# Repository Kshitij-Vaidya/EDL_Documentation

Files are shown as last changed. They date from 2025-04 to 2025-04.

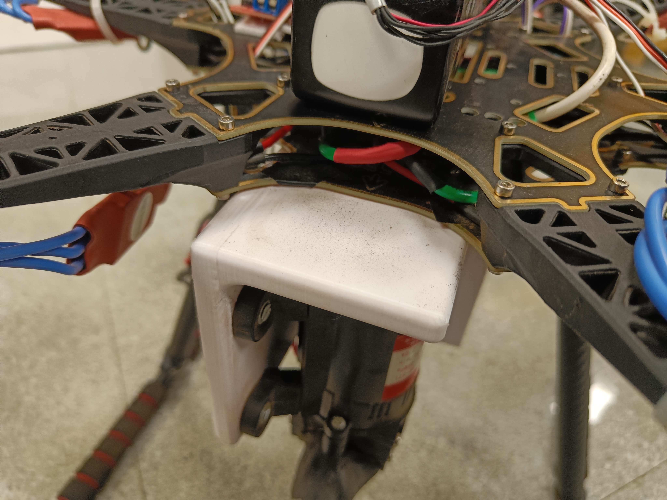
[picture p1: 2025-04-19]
others/assembly/close_up_motor_clamp.jpg

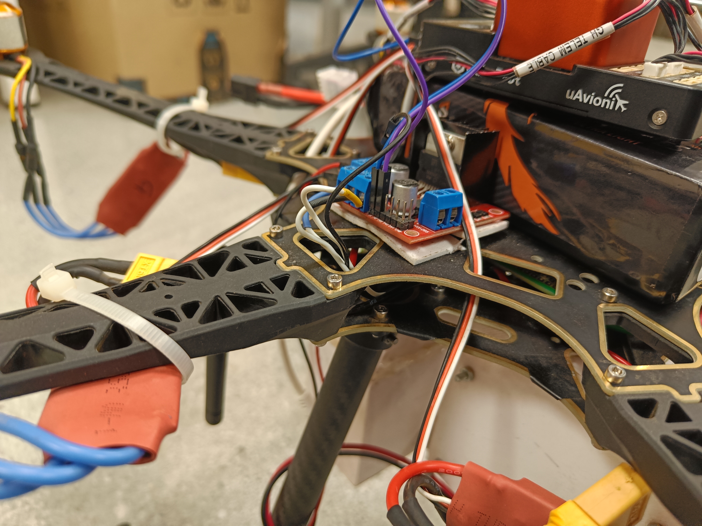
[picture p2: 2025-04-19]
others/assembly/arm_attachments.jpg

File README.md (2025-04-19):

# EDL 2025 Project Submission Repository

## Project Overview

### Project Name: P08 - Wall/Glass Pane Cleaning Drone
### Team Number: MON-13
### Team Members:
| Name | Roll No  |
|---|---|
| Aagam Shah | 22B1201  |
| Adit Srivastava | 22B1269  |
| Jainam Ravani | 22B1242  |
| Jay Mehta | 22B1281  |
| Kshitij Vaidya  | 22B1829  | 

<!-- ### Problem Statement and Solution: -->

## Problem Statement 
1. Build an aerodynamically stable drone for cleaning high-rise building windows.  
2. Ensure it can withstand windy conditions and recoil from high-pressure water spraying.  
3. Carry sufficient water to clean multiple windows.  
4. Operate safely in both manual and autonomous modes.  

## Proposed Solution

Our system consisted of a water spraying mechanism integrated with a baseline drone model. The spraying mechanism comprises of an onboard pump capable of ejecting water at 3L/min, which when coupled with our chosen nozzle suffices to clean dust and grime from glass surfaces, and a water tank that can either store enough water for the mission or utilize a continual water supply from a ground pump.

### Hardware Design Choices

In order to sustain the additional payload, we used an S550 hexacopter frame; the specs of various components including the BLDC motors and propellers were decided so as to achieve stable hover at 50% throttle. Pixhawk Cube flight controller equipped with PX4 Autopilot was used for regulating motor speeds to achieve a controlled flight. Various flight modes of the PX4 Autopilot were used to achieve manual as well as semi-autonomous navigation. Manual operation consisted of navigating the drone using roll, pitch, yaw and throttle setpoints from a Radio Controller; whereas the autonomous mode consisted of navigating to prespecified waypoints set by the user on the Ground Control Station (QGroundControl).

### QGroundControl Software

QGC proved to be instrumental not only for communication with the drone during flight but also for calibrating sensors, motor ESCs and updating flight parameters. For establishing connection with the Ground Control Station, we used a radio telemetry module. The state estimates of the drone required for autonomous navigation were determined using an external GPS module and onboard sensors on the flight controller. For remotely operating the spraying mechanism, an RC channel was assigned to regulate the voltage of the onboard pump.

An optimal choice of various PID gains for the flight controller ensured that our drone remained stable during flight, and maintained its position even in the presence of external disturbances like wind and recoil force of the spray. For aiding manual navigation, FPV control was added by using a Raspberry Pi and an onboard RPi-camera for transmitting continuous video streams to the ground control station. Further, all electrical components were insulated using a silicone spray and were mechanically protected by 3D-printed envelopes.

### Safety Measures

To ensure safety of the drone, surrounding structures, and the operating personnel, various failsafes were enabled including GPS signal loss failsafe, low battery failsafe, and radio signal loss failsafe. These failsafes ensured that in any of the aforementioned conditions, the drone returns safely to its launching site. In addition to this, a pipeline was established to allow users to upload custom missions or specify a set of waypoints, enabling cleaning of an entire structure with a single key press.

## Project Deliverables

1. A Hexacopter Drone with an onboard Pixhawk Cube, Telemetry Module, GPS Module and Radio Receiver 
2. A Complete Water Spraying Mechanism with a Water Tank, Water Pump and a Spraying Pipe with a Nozzle for Effective Water Spraying
3. Complete Software Stack for operating the Drone using Radio Control as well as for autonomous takeoff and hover in various operating modes like Position and Hold.  

## Navigating the Repository

```plaintext
/
├── src/
│   ├── Controller 1
|   ...
├── 3d_models/
│   ├── Component 1
│   ...
├── pcb/
│   ├── others/
├── reports/
├── others/
├── bom.xlsx
└── README.md
```

The repository includes all the essentials needed to understand and replicate this project in its current state. We have also highlighted our learnings, the mistakes we have made and the solutions and workarounds that we have found. 

1. The `src` folder includes the details of our Pixhawk, Raspberry Pi and the Radio Control that we have used. Their respective `README.md` files include instructions of using them and what changes we made to their default configurations before operating them.
2. The `3d_models` directory has all our CAD Models with their renders and the images of final fabricated components. We also include our insights about each of these components and design choices(if any) that went into finalising said components.
3. While we did not design and fabricate a PCB, the `pcb` directory includes a single directory `others` that has the designs and implementations and schematics of our in-house Power Distribution Board and the BEC Circuit that we have installed on our current prototype.
4. `reports` includes all our checkpoint presentations. This directory serves as a progress tracker for our project which indicates the levels of completion of our drone at various stages of the semester.
5. We include our simulation results and images of our assembly in parts and as a whole in the `others` directory. 
6. The `bom.xlsx` is our complete Bill Of Materials where we provide the list of components that have been procured for the project. We have also provided links and references for purchase from official and authentic sources.    

## Learnings and Key Takeways

1. Developed an understanding on aerial robotics (specifically quadcopters and hexacopters) from a mechanical point of view. This was crucial in making the choice between a quadcopter and hexacopter for out final drone. We eventually settled on the latter because of its increased payload capacities.
2. Working with the Pixhawk Cube as our Primary Flight Controller. This was a unique challenge as despite the Pixhawk being an off-the-shelf state of the art controller, we ran into multiple techincal and compatibility issues that needed to be resolved. We also needed to re-configure the boot sequence of the Pixhawk to ensure that our ESC Calibration and power up was synchronised
3. Electronic Speed Controllers must be thoroughly tested before installation on the drone. We faced severe troubles with the calibration of our ESCs partly because of the faults in the ESCs themselves and partly because of their improper calibration with the flight controller
4. Power Distribution Boards are extremely crucial in robotics applications. Our on-frame PDB was not uniformly powering the ESCs causing them to shut down unexpectedly. This also cost us one of our ESCs as it shut down during testing and we were unable to get it working again. To resolve this issue, we developed and made our own PDB using single sided copper clads and multi-stranded PVC wire.  
5. Experimented with different methods of operating the drone including Radio Control, using the QGroundController and operating the actuators from a laptop communicating with the drone using a Telemetry Module. These were especially useful for continuous testing and dry testing the components before performing the flight tests
6. Beyond the technical learnings, this project also helped us improve our time management and team skills. Coordinating with other members to ensure that the project keeps moving forward and our progress is not halted. We also learned that tasks should not be trivialized or underestimated. We made this mistake with our assembly and calibration but ran into a large number of errors because of both our mistakes and the malfunctions of our components. 

## Road Ahead

In the semester long project, we were able to develop a proof of concept prototype for the window cleaning drone but there are several areas of improvement that we have identified which would make this project even better:

1. Our current payload capacity is around 2kg which includes a 0.5L water tank. This is not sufficient for sustained cleaning purposes and we need to increase the total water carrying capacity of the drone. This can be done in 2 ways : increasing the water tank capacity or using a ground stationed water pump to supply water to the drone. Both these methods can be experimented with, each has their advantages and disadvantages which must be weighed carefully.
2. We can use motors with an inceased KV Rating. This increases the total thrust that is provided by the motors and thus increases the payload capacity of the drone. While this comes at the cost of a decreased battery life, the analysis of the decision must be done by weighing all options such as exploring the possiblility of using a larger battery
3. The whole drone system can be scaled by in size. While the weight of the drone frame does increase, this can be offset by using larger batteries and more powerful motors. This also facilitates a larger water tank which can be installed on-board. (In the current marker agricultural and irrigation drones which work on similar principles have payloads of upto 10-16L of fluid)
4. Implement a user-friendly Graphical User Interface Application that can be used to input the coordinates of the windows as waypoints with approximate window sizes. An on-board computer converts these into a mission which can be run by the drone to clean the windows at the waypoints in succession. 
5. We can modify and explore robust controllers which provide additional stability to the drone and improve the performance of the drone in windy conditions and handle the recoil and other forces by the water mechanism in a better manner

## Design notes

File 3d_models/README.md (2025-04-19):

# 3D Models
## File Structure

```
3d_models/
├── Canopy/
│   ├── canopy.png
│   ├── canopy.stl
│   └── README.md
├── Clamp for Diaphragm Pump/
│   ├── diaphragm_pump_clamp.png
│   ├── diaphragm_pump_clamp.stl
│   └── README.md
├── PixHawk_Casing/
│   ├── pixhawk_casing.png
│   ├── pixhawk_casing.stl
│   ├── Section-Analysis.png
│   └── README.md
├── Raspberry Pi Casing Bottom/
│   ├── rpi_casing_bottom.png
│   ├── rpi_casing_bottom.stl
│   └── README.md
├── Raspberry Pi Casing Top/
│   ├── rpi_casing_top.stl
│   ├── rpi_casing_top.png
│   └── README.md
├── Tank_Container/
│   ├── tank_container.png
│   ├── tank_container.stl
│   └── README.md
└── Tank_Cover/
    ├── tank_cover.png
    ├── tank_cover.stl
    └── README.md
```

## Material Used
ABS is used for all the models as it is significantly stronger than PLA and water doesnt seep through it as much as it does through ABS thus helping us make water-tight container. We had used PLA initially for some models but it wasn't very strong.

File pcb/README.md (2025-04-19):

# PCB Directory

This directory is named for convention but **does not contain any PCB (Printed Circuit Board) design files**, as our project does not utilize traditional PCBs.

Instead, we have developed:
- An **in-house Power Distribution Board (PDB)** tailored specifically for our drone’s power routing needs.
- A **custom Battery Eliminator Circuit (BEC)** to efficiently provide regulated voltage to onboard components.

All power management is handled through these custom solutions, allowing for greater flexibility and simplified integration with our drone architecture.

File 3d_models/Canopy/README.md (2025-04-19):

## Canopy

### Placement
The canopy is mounted directly above the top plate of the drone and is secured using adhesive(double-sided) tape applied to the top plate.

### Function
- **Protection:** It safeguards the upper components of the drone from physical impact, dust, and water ingress.
- **Aerodynamics:** It contributes to improved aerodynamic performance by streamlining the top surface of the drone.

### Material
Constructed from **ABS (Acrylonitrile Butadiene Styrene)**, a durable and impact-resistant thermoplastic ideal for lightweight protective applications.

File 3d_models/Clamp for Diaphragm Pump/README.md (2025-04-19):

## Clamp for Diaphragm Pump

### Placement
This is an L-shaped clamp designed with one face mounted to the bottom plate of the drone, while the other face secures the diaphragm pump in an upright position.

### Function
The clamp’s sole function is to provide firm and stable support for the diaphragm pump, ensuring it remains upright during operation.  
To withstand mechanical stress and potential impact, the clamp is printed with **100% infill**. This structural density is critical, as previous iterations with lower infill failed under impact conditions.

### Material
Manufactured from **ABS (Acrylonitrile Butadiene Styrene)** for its high strength, durability, and impact resistance.

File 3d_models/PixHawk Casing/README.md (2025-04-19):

## PixHawk Casing

### Placement
The casing is designed to fit securely over the PixHawk flight controller. The square cavity is dimensioned to enclose the PixHawk Cube precisely.

### Function
- **Protection:** Shields the PixHawk Cube from physical damage.
- **Stability:** Helps keep the flight controller securely in place during operation.
- **Dust Prevention:** Covers the exposed ports of the PixHawk, reducing the risk of dust ingress.

### Material
Fabricated from **ABS (Acrylonitrile Butadiene Styrene)**, chosen for its robustness, durability, and impact resistance.

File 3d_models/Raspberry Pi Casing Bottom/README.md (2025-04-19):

## Raspberry Pi 4 Casing — Bottom

### Placement
The Raspberry Pi 4 is mounted into this bottom casing and secured using nuts and bolts. Side extrusions are incorporated into the design to interlock with the top part of the casing, ensuring a snug fit.

### Function
- **Protect** the Raspberry Pi 4 from impact damage during drone operation.
- **Secure** the Raspberry Pi 4 firmly in place using fasteners, preventing internal movement that could lead to hardware damage.

### Material
Constructed from **ABS (Acrylonitrile Butadiene Styrene)**, selected for its high impact resistance and structural integrity.

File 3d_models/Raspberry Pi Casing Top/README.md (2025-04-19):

## Raspberry Pi 4 Casing — Top

### Placement
This component fits directly on top of the Raspberry Pi 4, forming the upper half of the protective enclosure. It includes dedicated slots to accommodate the ribbon cable of the Raspberry Pi NoIR Camera.

### Function
- **Protect** the Raspberry Pi 4 from impact and environmental exposure.
- **Allow Connectivity** by providing access points for the NoIR Camera ribbon strip without compromising enclosure integrity.

### Material
Made from **ABS (Acrylonitrile Butadiene Styrene)**, chosen for its durability, impact resistance, and suitability for electronic housings.

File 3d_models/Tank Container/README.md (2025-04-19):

## Tank Container

### Placement
The tank container is affixed to the bottom rim of the tank cover using adhesive. A hole is drilled at the base of the container to accommodate an extrusion, which connects to the pipe leading to the diaphragm pump.

### Function
This component functions as the **primary water storage unit** for the drone. Its dimensions are constrained by:
- **Payload capacity** of the drone
- **Ground clearance** to ensure safe landing and operation

### Material
Fabricated from **ABS (Acrylonitrile Butadiene Styrene)** for its strength and moldability.  
A **conformal coating spray** is applied to the interior surface to ensure the container is both **water-proof** and **water-tight**.

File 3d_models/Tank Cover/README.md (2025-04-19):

## Tank Cover

### Placement
The tank cover is mounted on top of the tank container and is glued along the rim for a secure seal. It is further attached to the drone’s bottom plate using **2 cm spacers**, providing structural stability and elevation.

### Function
- **Seals** the tank container to prevent water leakage.
- **Provides Access** through a dedicated hole for filling the tank with water.

### Material
Constructed from **ABS (Acrylonitrile Butadiene Styrene)**.  
An internal application of **conformal coating spray** ensures the component is **water-proof** and **water-tight**, maintaining the integrity of the onboard water storage system.

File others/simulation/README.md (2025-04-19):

Before performing hardware tests, we validated our approach on simulation.

## Software Requirements
- Gazebo Classic : https://docs.px4.io/main/en/sim_gazebo_classic/index.html
- ROS2 : https://docs.ros.org/en/humble/Installation.html
- MicroXRCE DDS : https://micro-xrce-dds.docs.eprosima.com/en/latest/agent.html
- Plotjuggler : https://index.ros.org/p/plotjuggler/
- Python : Version 3.10 or higher
- QGroundcontrol : https://docs.qgroundcontrol.com/master/en/qgc-user-guide/getting_started/download_and_install.html

## Gazebo Simulator
Gazebo Classic is a powerful, open-source 3D robotics simulator that integrates with ROS (Robot Operating System) and allows realistic testing of robots in complex environments. It provides physics simulation (via engines like ODE, Bullet), sensor simulation (e.g., cameras, IMUs, lidars), and supports plugins for custom behavior. For simulating our system, we used a default hexacopter model available in PX4's software stack, and varied its physical parameters according to our hardware specifications. Some of these values are:

### Inertial Parameters

| Component | Dimensions | Mass  | MoI (Ix) | MoI (Iy) | MoI (Iz) |
|---|---|---|---|---|---|
| Chassis | 0.67 x 0.67 x 0.15 | 0.997  | 0.039 | 0.039 | 0.075 |
| Camera | 0.01 x 0.01 x 0.01 | 0.011  | 1.83e-7 | 1.83e-7 | 1.83e-7 |
| Landing Legs  | 0.01 x 0.03 (r x h) | 0.1 | 7.54e-4 | 7.54e-4 | 7.45e-3 |
| Rotors | 0.128 x 0.005 (r x h)  | 0.024  | 9.83e-5 | 9.83e-5 | 1.97e-4 |
| Nozzle | 0.05 x 0.12 (r x h) | 0.05 | 0.07 | 0.07 | 0.07 |

### Motor Parameters

| Parameters | Value |
|---|---|
| Time Constant (s) | 0.0125 |
| Max Speed (rad/s) | 1240 |
| Max Speed (RPM) | 11840 |
| Motor Constant (N·s²/rad²) | 8.038e-6 |
| Moment Constant (N·m·s²/rad²) | 9.55e-3 |
| Rotor Drag Constant | 0.09637 |
| Rolling Moment Coefficient | 1e-6 |

## Simulation Environment
- Simulator: Gazebo Classic
- Drone Model: Typhoon H480 (with custom parameters)
- Autopilot: PX4 v1.14
- Middleware: ROS2 with MicroXRCE bridge
- Operating System: Ubuntu 22.04

## Objective
- Take off the drone and maintain a constant altitude for 10s.
- To start spraying water in the specified direction.
- To ascend upwards by some distance while spraying water and
then stabilizing at its original altitude

## ROS2
We used ROS2 as the middleware for using the offboard mode on our simulated drone. A ROS2 node was run in the form of a python script after launching the drone. This node essentially utilized gazebo-ros topics for applying user-specified forces on the drone model. For bridging ROS2 with Mavlink (used by PX4 for communication), we used MicroXRCE-DDS.

## Water Spray Test
For simulating weight of the water column, reaction and recoil forces we applied forces in horizontal and vertical directions when the drone attained a stable altitude. The aforementioned script applied a constant vertical force simulating the weight of the onboard tank/ water column, and a user specified horizontal (with respect to drone frame) force on the drone.

## Running the Simulation
Expected configuration:
- All required softwares are installed
- Latest version of PX4 Autopilot repository is cloned and built
- A ROS2 workspace is setup with px4_msgs and px4_ros_com repositories cloned in the source directories
- The python file simulation.py is copied in the px4_ros_com folder
- MicroXRCE-DDS agent is cloned and built
- Parameters of the TyphoonH480 drone are modified as mentioned above

Run the following commands in separate terminals:

1. `./<path-to-QGC>/QGroundControl.AppImage`
2. `MicroXRCEAgent udp4 -p 8888`
3. `make /<path-to-PX4>/PX4-Autopilot/px4_sitl_default gazebo_typhoon_h480`
4. `ros2 run /<path-to-simulation.py>/simulation.py`

First takeoff the drone using QGC and let it stabilize. Then enter force values you want to simulate in the terminal running simulation.py. Finally, close all the terminals, extract the log file(.ulg) for the run for further analysis.

## Results and Analysis

Log files for the entire mission were analyzed and graphs were plotted using Plotjuggler. 

For force simulation, we computed the recoil thrust and an approximate value of the downward force using flow rate and mass of the tank/pipe and water pump that we used. We took the maximum value of these forces which were 10N in the horizontal and 11N in the Z direction.

From the position plots that we obtained, we inferred that the drone suffered an average perturbation of 0.3m in the horizontal direction and an average altitude drop of 0.2m once drone starts spraying water. Moreover, the drone settles at a pitch of around 20 degrees. Settling time for our run was around 5s.

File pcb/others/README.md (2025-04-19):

## Contents:
- `bec_rpi_motor.png`
- `bec_rpi_motor.ps`
- `bec.jpg`
- `motor_driver.jpg`
- `pdb_pixhawk.png`
- `pdb_pixhawk.ps`
- `pdb.jpg`
- `pixhawk_pins.jpg`
- `pixhawk_telem_gps.jpg`

## Description

1. `bec_rpi_motor.png`: Circuit Diagram for the connections between the Battery Eliminator Circuit (BEC), Raspberry Pi 4 and Diaphragm Motor.

2. `bec_rpi_motor.png`: Post-Script file generated by X-Circuit which is converted to .png.

3. `bec.jpg`: Actual photo of circuit implementation of the general purpose PCB on which the BEC is attached.

4. `motor_driver.jpg`: Actual photo of the connections to the motor driver.

5. `pdb_pixhawk.png`: Circuit Diagram for the PixHawk and the Power Distribution Board.

6. `pdb_pixhawk.ps`: Post-Script file generated by X-Circuit which is converted to .png.

7. `pdb.jpg`: Actual photo of the Power Distribution Board used in the drone. 

8. `pixhawk_pins.jpg`: Pin connections to the PixHawk. This includes RC connections, ESC connections to PWM Main and the Motor Driver connection to PWM AUX.

9. `pixhawk_telem_gps.jpg`: Connections of the Telemetry and GPS Module to the PixHawk.

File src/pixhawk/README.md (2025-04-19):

# Pixhawk Cube Orange+

## Hardware Specifications

Pixhawk Cube Orange+ is used as our flight controller unit. It is used primarily because of it's compatibility with a large range of autopilots, especially PX4. 

### Primary Sensors                     

Following lists some specs of our chosen flight controller:

1. Processor & Co-Processor
    - Main Processor: STM32H757ZI (32-bit ARM Cortex-M7) running at 400 MHz
    - Failsafe Co-Processor: STM32F103 (32-bit ARM Cortex-M3) operating at 24 MHz

2. Sensors
    - Accelerometers: 3 redundant units (ICM42688p, ICM20948, ICM20649)
    - Gyroscopes: 3 redundant units (ICM42688p, ICM20948, ICM20649)
3. Magnetometer: 1 unit (ICM20948)
4. Barometers: 2 units (MS5611)

### Additional Sensors

These sensors are connected via SPI and are housed in a temperature-controlled, vibration-isolated enclosure to ensure optimal performance.
1. Power Management
    - Redundant Power Supply: Dual inputs with automatic failover
    - Servo Rail Voltage: Supports 3.3V and 5V (software-selectable)
    - Input Voltage Range: 4.1V to 5.7V

    - Rated Input Current: 2.5A

    - Rated Input/Output Power: 14W

2. USB Port Input: 4V to 5.7V, 250 mA

3. I/O & Communication Ports
    - PWM/Servo Outputs: 14 total (8 from IO, 6 from FMU)

    - UART Ports: 5 total (1 high-power capable, 2 with hardware flow control)

    - CAN Bus Interfaces: 2 (1 with internal 3.3V transceiver, 1 on expansion connector)

    - R/C Inputs: Supports Spektrum DSM/DSM2/DSM-X® Satellite, Futaba S.BUS®, and PPM-SUM

    - RSSI Input: PWM or voltage

    - I2C Ports: 2

    - SPI Port: 1 (un-buffered, for short cables only)

    - Analog Inputs: 3 (3.3V and 6.6V)

    - USB Ports: Internal microUSB and external microUSB extension

4. Additional Features
    - Failsafe Co-Processor: Ensures system reliability during critical operations

    - Integrated Backup System: Facilitates in-flight recovery and manual override, especially beneficial for fixed-wing applications

    - Redundant Power Supply Inputs: Automatic failover to maintain system stability

    - External Safety Switch: For manual intervention and safety

    - Multicolor LED Indicator: Provides visual status feedback

    - High-Power, Multi-Tone Piezo Audio Indicator: Audible alerts for system status

    - microSD Card Slot: Supports high-rate logging over extended periods

## Reasons for Choosing PX4 Autopilot

We proceeded with the PX4 Autopilot over other autopilots for the following reasons:
- It's largely used by industries and hobbyists around the world, with a large community of developers, ensuring a consistently stable performance.

- The source code is fairly modular and is accompanied with a comprehensible documentation, which could have allowed us to integrate our custom controller code into the PX4 architecture seamlessly, had we chosen to do so.
- There is a wide range of tunable parameters that we could customize to ensure an optimal system performance.
- There exist multiple failsafes including low battery, telemetry loss and gps loss failsafes, ensuring that the drone returns safely to its takeoff position.
- It is compatible with a wide range of middlewares like ROS, allowing the user offboard applications like carrying out entire missions.
- It's compatibility with middlewares also allowed us to validate its performance on physics simulating platforms like Gazebo prior to performing hardware tests. 

## Review of PX4 Software Stack

The latest version of the PX4 autopilot was cloned from the following source: https://github.com/PX4/PX4-Autopilot

Initially, in order to explore possibilities of changes that we could make to the source code in order to integrate our controller, we thoroughly reviewd the PX4 stack and identified the relevant modules and uORB topics that needed to be modified for incorportating out scheme. The following lists these modules:

- `mc_pos_control`: This module of PX4 is responsible for implementing the position and velocity controllers and transforming the PID controlled accelerations by a rotation matrix to output the desired attitudes as quaternions. In addition, it computes the desired thrust in the body frame for the nominal case. Since the outer-loop control is independent of the configuration and the number of rotors of the aerial vehicle, we leave it unchanged for our implementation. The roll and pitch setpoints used by the default attitude controller are the same as the ones used for our custom control strategy.

- `mc_att_control`: This module implements the attitude control (the first part of the inner loop). The default controller subscribes to the attitude setpoints published by the mc_pos_control and performs non-linear quaternion-based attitude control to compute the rate setpoints. The function responsible for this computation is the `AttitudeControl::update()` function, defined in the `mc_att_control`/`AttitudeControl.cpp` file, which is called at every iteration of `mc_att_control::Run()`. For our custom implementation, we compute the actuator setpoints (normalized motor thrust values) in this module itself. We create the `AttitudeControl::custom_update()` function to publish actuator commands to the mixer module. This switching is controlled by the failure detector module. Moreover, rate setpoints are not published in the case of a motor failure, bypassing the default rate and control allocator modules.

- `mc_rate_controller`: This module performs PID control on the angular body rates to compute the commanded thrust and torques. For our implementation, we have bypassed this module since all of our inner loop computations are being performed in the attitude control module itself.

- `control_allocator`: Thrust and torque setpoints are pre-multiplied by the control effectiveness matrix to calculate the normalized motor thrusts. Since our attitude controller module, in its custom mode of implementation, publishes actuator setpoints as well, a potential collision of setpoints is prevented by a conditional statement controlled by the failure detector module.

Since the tests we performed on simulation depicted that the drone remained reasonably stable despite the recoil forces it experienced from the water spraying mechanism using the default cascaded PID flight controller, we didn't feel the need to explore other advanced controllers and subsequently make changes to the source code.

## Pixhawk Flight Modes

### Pixhawk Flight Modes Explained

Pixhawk supports various flight modes, each suited for different flying styles and purposes. Below is a detailed explanation of commonly used modes:

---

#### 1. **Manual Mode**

- **Description**: 
  - Pilot has **full control** of the aircraft.
  - No stabilization or assistance from the flight controller.

---

#### 2. **Stabilized Mode**

- **Description**:
  - The flight controller automatically **levels the aircraft** when sticks are centered.
  - Pilot controls throttle and direction manually.

---

#### 3. **Altitude Mode**

- **Description**:
  - The aircraft **maintains a consistent altitude** using barometer data.
  - Pilot controls roll, pitch, and yaw.

---

#### 4. **Hold Mode**

- **Description**:
  - Aircraft holds **current GPS position and altitude**.
  - Re-centering sticks will bring the aircraft to a stop and hover.

---

#### 5. **Acro Mode**

- **Description**:
  - Pilot controls **rotation rate**, not angle.
  - Aircraft does **not auto-level**.

---

#### 6. **Mission Mode**

- **Description**:
  - Executes a **predefined autonomous mission** using waypoints.
  - No manual input required during the mission.

---

#### 7. **Position Mode**

- **Description**:  
  - **Full position and altitude stabilization**
  - Uses **GPS and altitude sensors** to control the vehicle’s position and height.

---

> **Note**: Always ensure good **GPS lock** before using GPS-dependent modes like **Hold**, **Position** and **Mission**. Use **Manual or Stabilized** when testing indoors or in GPS-denied areas.

## Modifications to Base Software Stack Parameters

The only changes in the PX4 Autopilot were a result of changes made to the defult parameters. Here is an exhaustive list of all the parameters we changed:

1. Airframe parameters:
    - CA_AIRFRAME: Multirotor
    - MAV_TYPE: Hexarotor
2. Motor assignments:
    - PWM_MAIN_FUNC1: Motor 5
    - PWM_MAIN_FUNC2: Motor 1
    - PWM_MAIN_FUNC3: Motor 4
    - PWM_MAIN_FUNC6: Motor 6
    - PWM_MAIN_FUNC7: Motor 2
    - PWM_MAIN_FUNC8: Motor 3
3. RC setup:
    - RC_MAP_PITCH: Channel 2
    - RC_MAP_ROLL: Channel 3
    - RC_MAP_THROTTLE: Channel 1
    - RC_MAP_YAW: Channel 4
    - RC_MAP_AUX1: Channel 10
    - RC_MAP_ARM_SW: Channel 9
    - RC_MAP_FLTMODE: Channel 5
    - RC_MAP_KILL_SW: Channel 6
    - COM_FLTMODE1: Position
    - COM_FLTMODE4: Manual
    - COM_FLTMODE6: Hold
4. Disabling redundant failsafes:
    - COM_ARM_HFLT_CHK: Disabled
    - COM_ARM_SDCARD: Disabled
5. Changing min and max of pump pwms:
    - PWM_AUX_MIN1: 0
    - PWM_AUX_MAX1: 2000
6. Battery:
    - BAT1_N_CELLS: 4S Battery
    - BAT1_V_CHARGED: 4.20 V
    - BAT1_V_EMPTY: 0.0V
7. GPS:
    - GPS_1_CONFIG: GPS 2

## Peripherals Used

PX4 Autopilot uses the Mavlink protocol to communicate with various onboard and offboard peripherals. The onoboard peripherals consist of the built in sensors within the flight controller listed before, while the offboard peripherals include:
1. **GPS Module**: GPS 2 Port : Cirocomm Active GPS Antenna
2. **Motor Driver Pwm Input**: AUX1 Port : L298N Motor Driver
3. **6 30A ESCs**: MAIN 1-3 and 6-8 Ports : SimonK 30A Electronic Speed Controller
4. **Telemetry module**: TELEM1 Port : HolyBro SiK Telemetry Module
5. **RC receiver**: RC-IN Port : RadioMaster TX16S
6. **Power connection**: POWER1 Port : Bonka 4S LiPo Battery

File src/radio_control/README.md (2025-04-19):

# Radio Controller : RadioMaster TX16S

The RadioMaster TX16S is a versatile 16-channel 2.4 GHz radio transmitter. The TX16S is compatible with OpenTX and EdgeTX firmware, offering extensive customization options. It includes USB-C charging, dual USB-C ports, external SD card support, and two UART expansion ports for future upgrades. The transmitter is powered by two 18650 Li-ion batteries or a 2S LiPo battery, providing long-lasting performance. 

We used the following Radio Model on the transmitter to map the channels to our desired outputs.

1. Channel 1 : THR 100% : Throttle
2. Channel 2 : ELE 50% : Pitch
3. Channel 3 : AIL 50% : Roll
4. Channel 4 : RUD 100% : Yaw
5. Channel 5 : SE : Controls Flight Modes
6. Channel 6 : SF : Kill Switch
7. Channel 9 : SG : Arm/Disarm the Drone
8. Channel 10 : S1 : Knob for Controlling the Motor

The percentages in the first 4 parameters control the sensitivity of the knob. These channel numbers must also reflect in the QGroundControl software which determines the channels used by the Pixhawk. If something is changed in the Radio Control, the same change must be done on the Pixhawk and vice versa.

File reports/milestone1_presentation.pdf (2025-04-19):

## EE344 :ElectronicDesign Lab

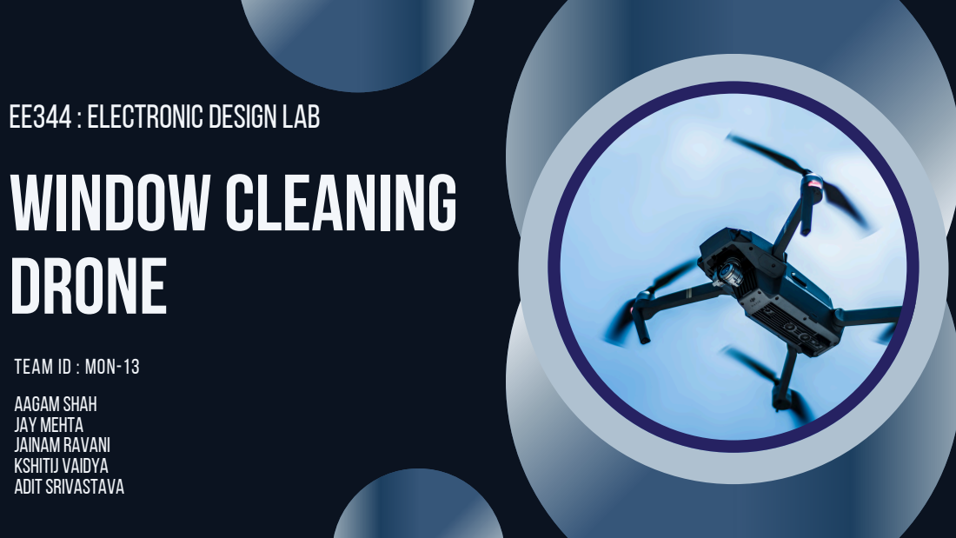
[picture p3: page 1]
Aagam Shah Jay Mehta Jainam RAvani Kshitij Vaidya AditSrivastava; Window Cleaning Drone

TEAM ID : MON-13

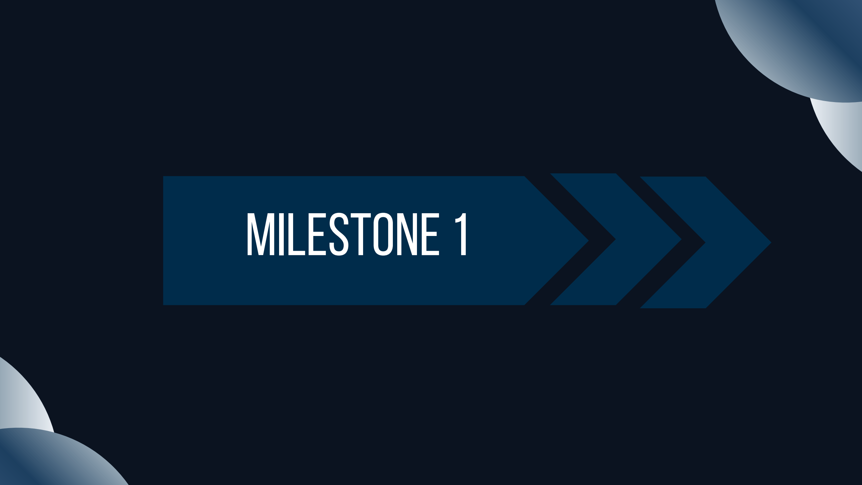
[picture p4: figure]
MiLEStONE1

# Challengesin Cleaning High-RiseWindows

Manual Effort and Risks: Cleaning windows of high-rise buildings is labor-intensive and involves significant safety risks for workers

Inefficiency: Traditional methods are time-consuming and require specialized equipment like scaffolding or
suspended platforms

High Costs: Employing skilled labor and safety measures increases operational expenses for building maintenance.

Environmental Challenges: Cleaning in adverse weather conditions or accessing hard-to-reach windows poses additional difficulties.

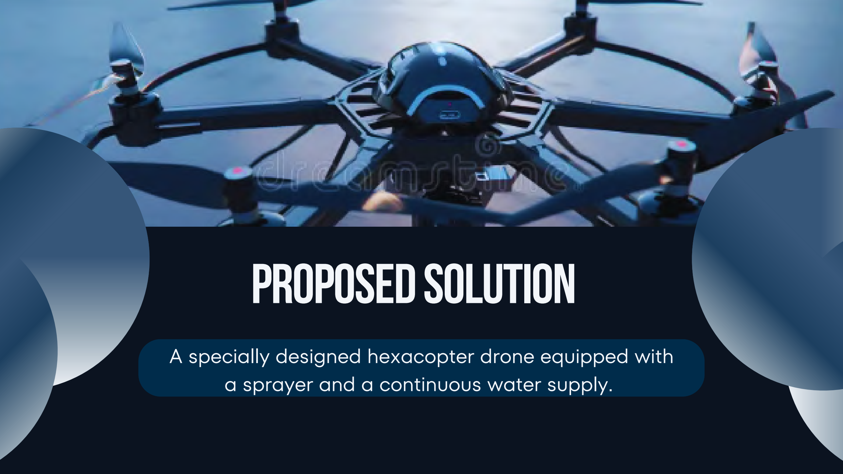
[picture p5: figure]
proposed solution

A specially designed hexacopter drone equipped with | a sprayer and a continuous water supply.

# Value Proposition

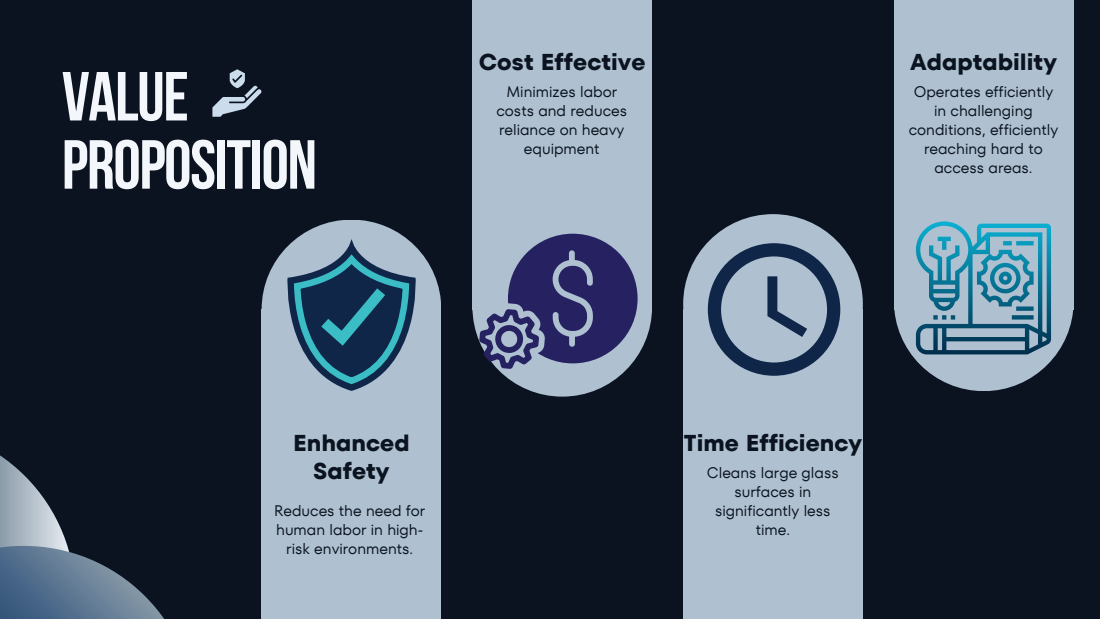
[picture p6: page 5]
Enhanced Safety; Time Efficiency; Cost Effective; Adaptability

Minimizes labor
costs and reduces
reliance on heavy
equipment

Operates efficiently
in challenging
conditions, efficiently
reaching hard to
access areas.

Cleans large glass
surfaces in
significantly less
time.

Reduces the need for
human labor in high-
risk environments.

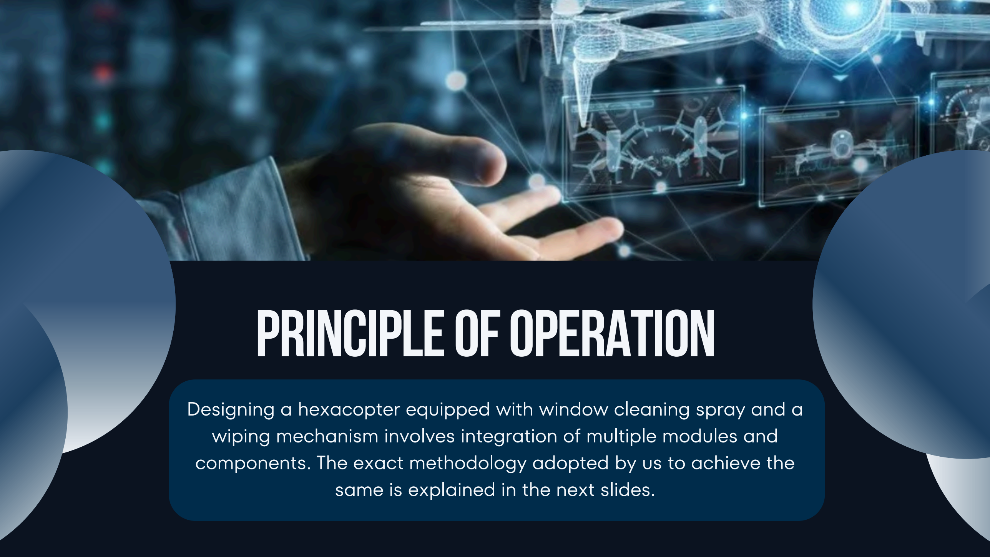
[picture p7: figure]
PrincipleofOperation

Designing a hexacopter equipped with window cleaning spray and a wiping mechanism involves integration of multiple modules and components. The exact methodology adopted by us to achieve the | same is explained in the next slides.

# methodology

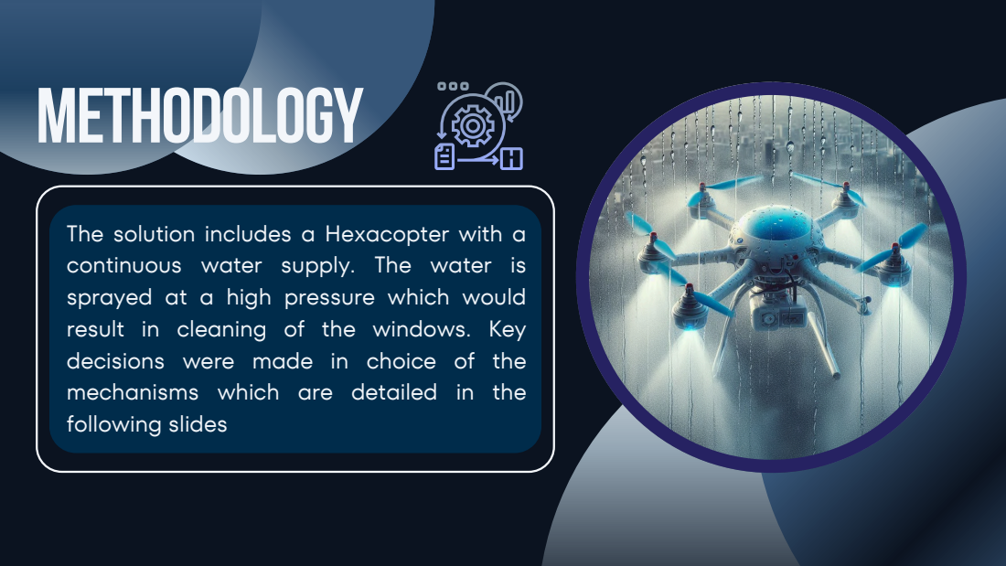
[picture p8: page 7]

The solution includes a Hexacopter with a
continuous water supply. The water is
sprayed at a high pressure which would
result in cleaning of the windows. Key
decisions were made in choice of the
mechanisms which are detailed in the
following slides

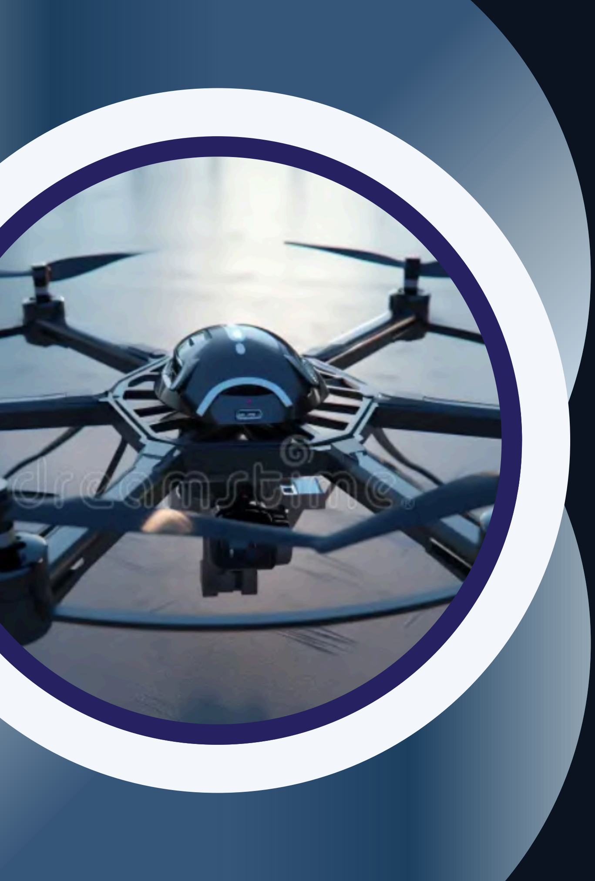
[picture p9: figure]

Making a Quad-copter is easier compared to a Hexacopter due to easier control over the Roll-Pitch-Yaw movements.
But a Hexa-copter increases the payload capacity due to a higher available thrust which is crucial since we need to house a motor and various transmitters on the drone.
For these reasons, a Hexa-copter was chosen over a Quad-copter despite the possible complexities

# quad vs hexa copter

# water supply vsstorage

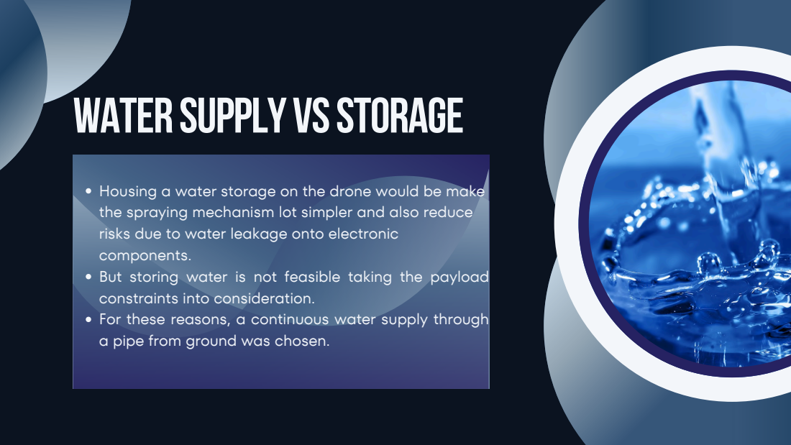
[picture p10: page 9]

Housing a water storage on the drone would be make
the spraying mechanism lot simpler and also reduce
risks due to water leakage onto electronic
components.
But storing water is not feasible taking the payload
constraints into consideration.
For these reasons, a continuous water supply through
a pipe from ground was chosen.

# groundmotor vson-board

For transferring water to the drone, we need a ground motor which can pump water till the drone’s height. But the pressure due to this motor won’t be significant enough to expel water at a high speed which is required for cleaning.
To tackle this we have installed a small DC motor on the drone which will increase the speed of the water before expulsion.

# TechNICAL Details

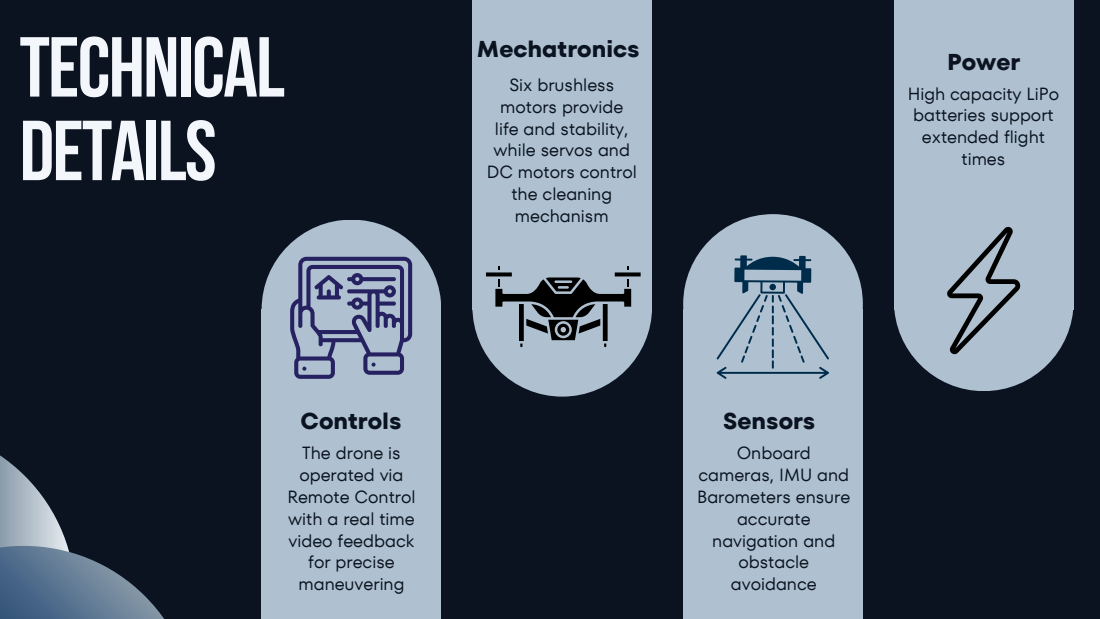
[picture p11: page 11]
Controls; Sensors; Mechatronics; Power

Six brushless
motors provide
life and stability,
while servos and
DC motors control
the cleaning
mechanism

High capacity LiPo
batteries support
extended flight
times

The drone is
operated via
Remote Control
with a real time
video feedback
for precise
maneuvering

Onboard
cameras, IMU and
Barometers ensure
accurate
navigation and
obstacle
avoidance

# TargetSpecifications

Parameter | Specifications

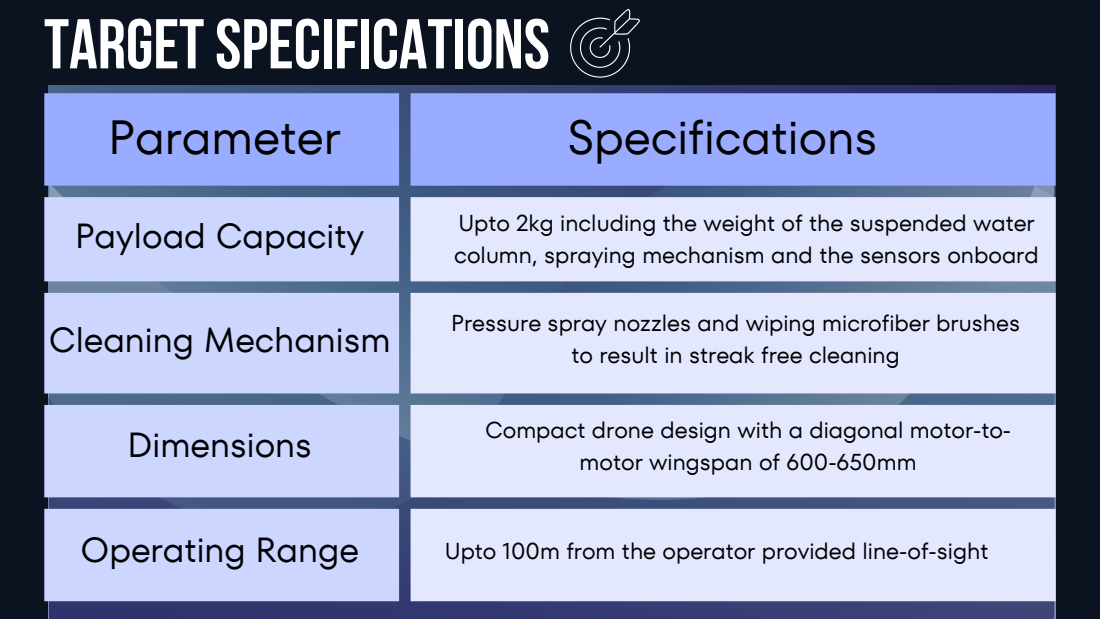
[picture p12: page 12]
Payload Capacity; Cleaning Mechanism; Dimensions; Operating Range; Upto 100m from the operator provided line-of-sight

Upto 2kg including the weight of the suspended water
column, spraying mechanism and the sensors onboard

Pressure spray nozzles and wiping microfiber brushes

to result in streak free cleaning

Compact drone design with a diagonal motor-to-

motor wingspan of 600-650mm

# Block Diagram

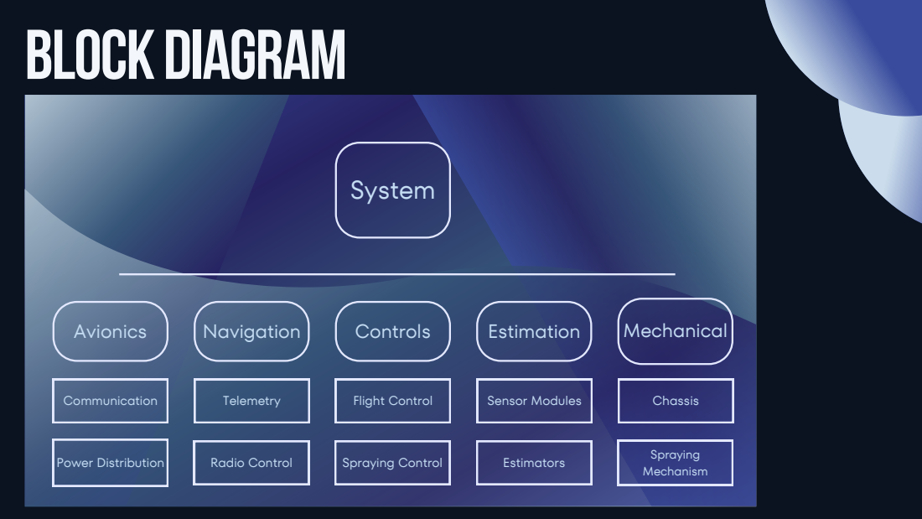
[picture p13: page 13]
System; Avionics; Navigation; Controls; Estimation; Mechanical; Communication; Power Distribution; Flight Control; Spraying Control; Sensor Modules; Estimators; Chassis; Spraying Mechanism; Telemetry; Radio Control

# circuit/data flowdiagram

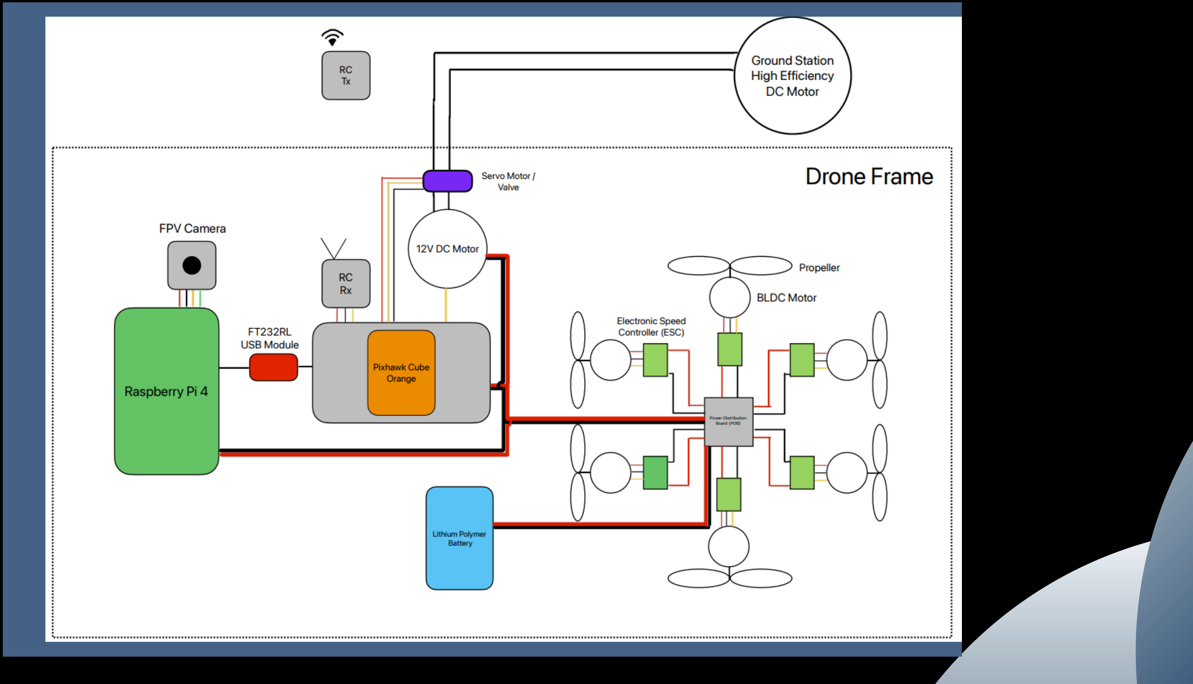
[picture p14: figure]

# BiLLOFMaterials

Component | Justification | Cost ( )

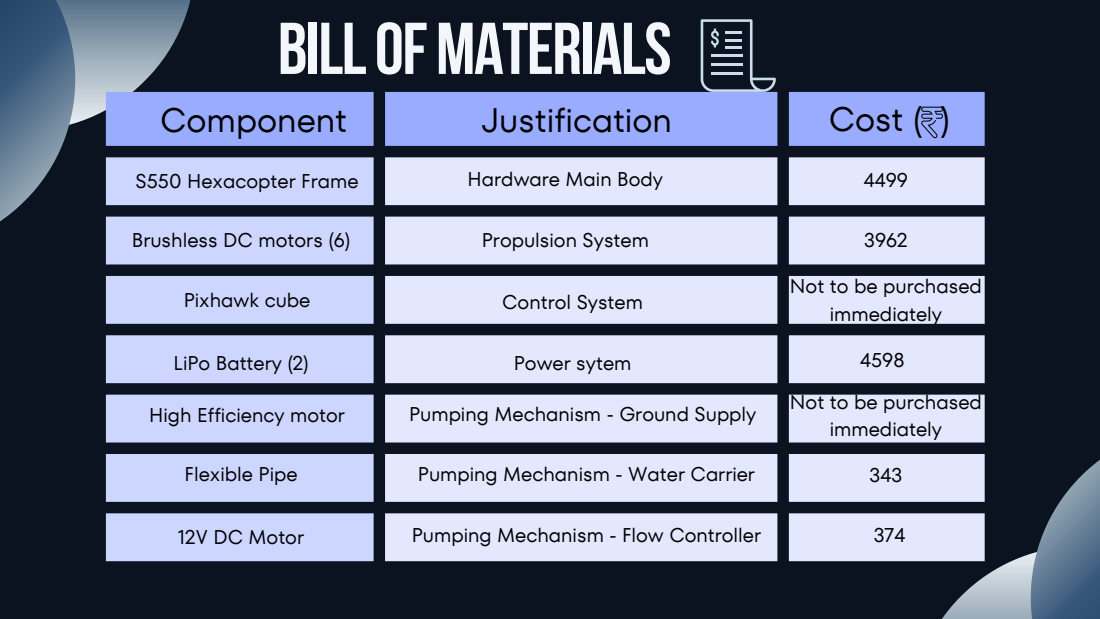
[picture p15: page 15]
S550 Hexacopter Frame; Hardware Main Body; Brushless DC motors (6); Propulsion System; Pixhawk cube; Control System; LiPo Battery (2); Power sytem; High Efficiency motor; Pumping Mechanism - Ground Supply; Flexible Pipe; Pumping Mechanism - Water Carrier; 12V DC Motor; Pumping Mechanism - Flow Controller

Not to be purchased
immediately

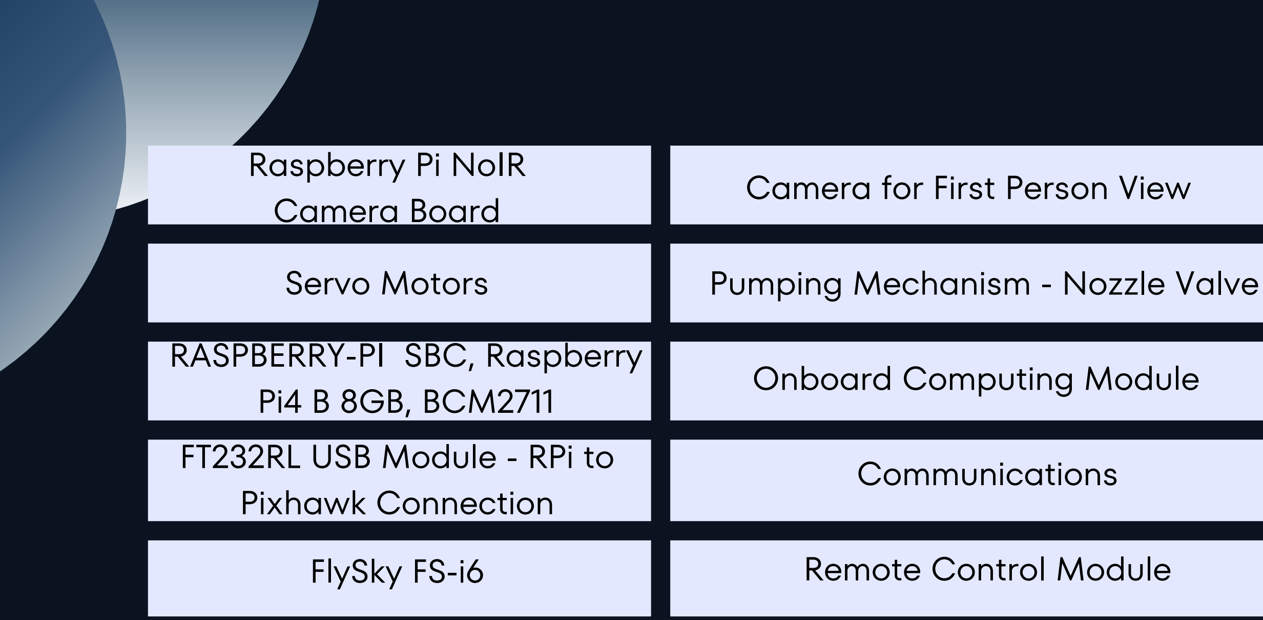
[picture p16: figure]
Raspberry Pi NoIR Camera Board; Camera for First Person View; Servo Motors; Pumping Mechanism - Nozzle Valve; RASPBERRY-PI SBC, Raspberry Pi4 B 8GB, BCM2711; Onboard Computing Module; FT232RL USB Module - RPi to Pixhawk Connection; Communications; FlySky FS-i6; Remote Control Module

Propeller Blades (6) | Hardware Component

In the EDL Inventory

In the EDL Inventory

In the EDL Inventory

319

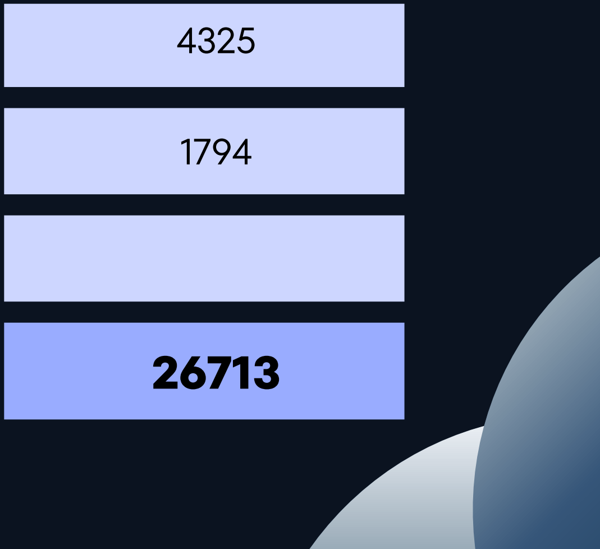
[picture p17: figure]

Total Cost :- | 26713

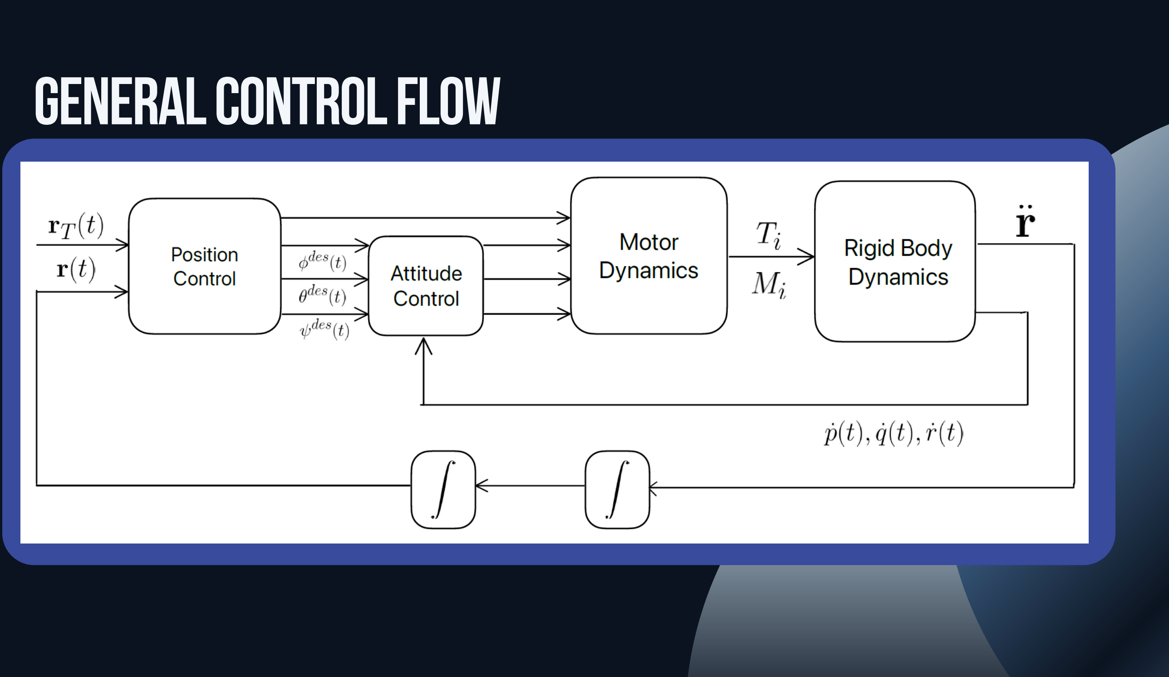
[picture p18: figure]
Generalcontrolflow

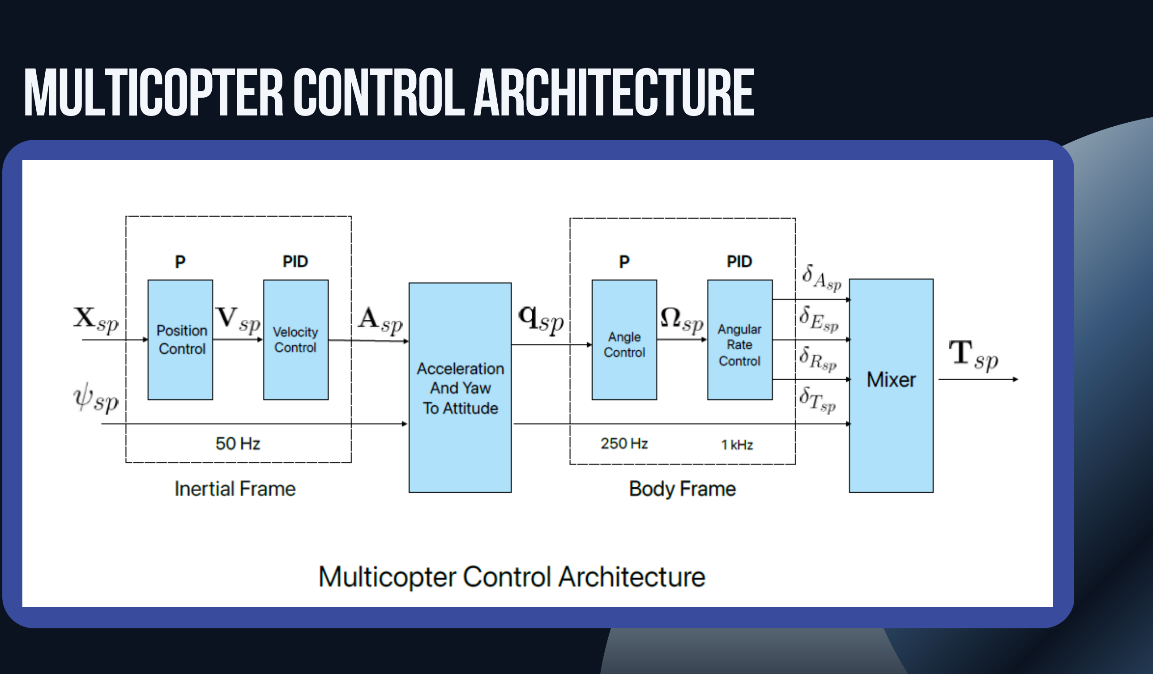
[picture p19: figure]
multicopter control architecture

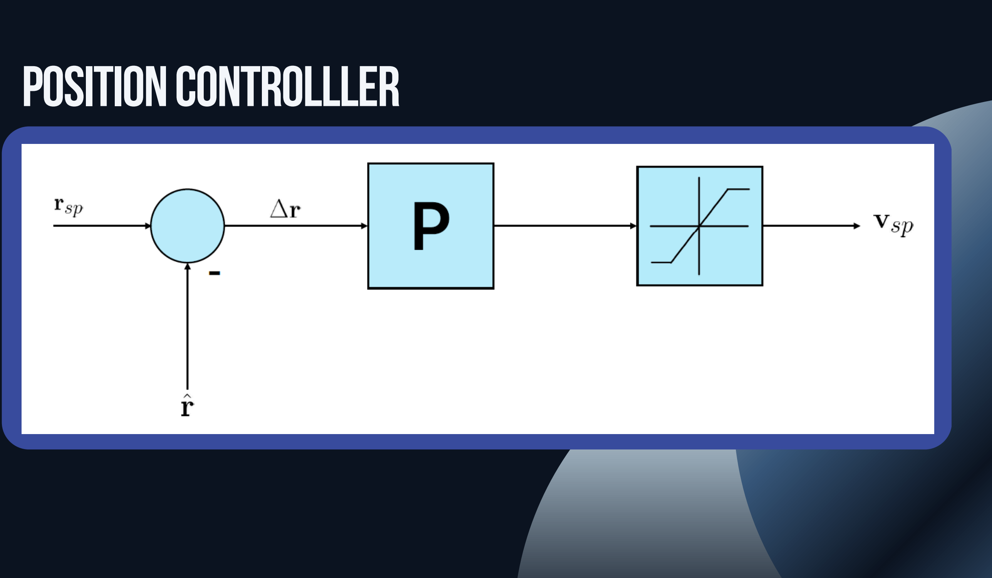
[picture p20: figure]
position controlller

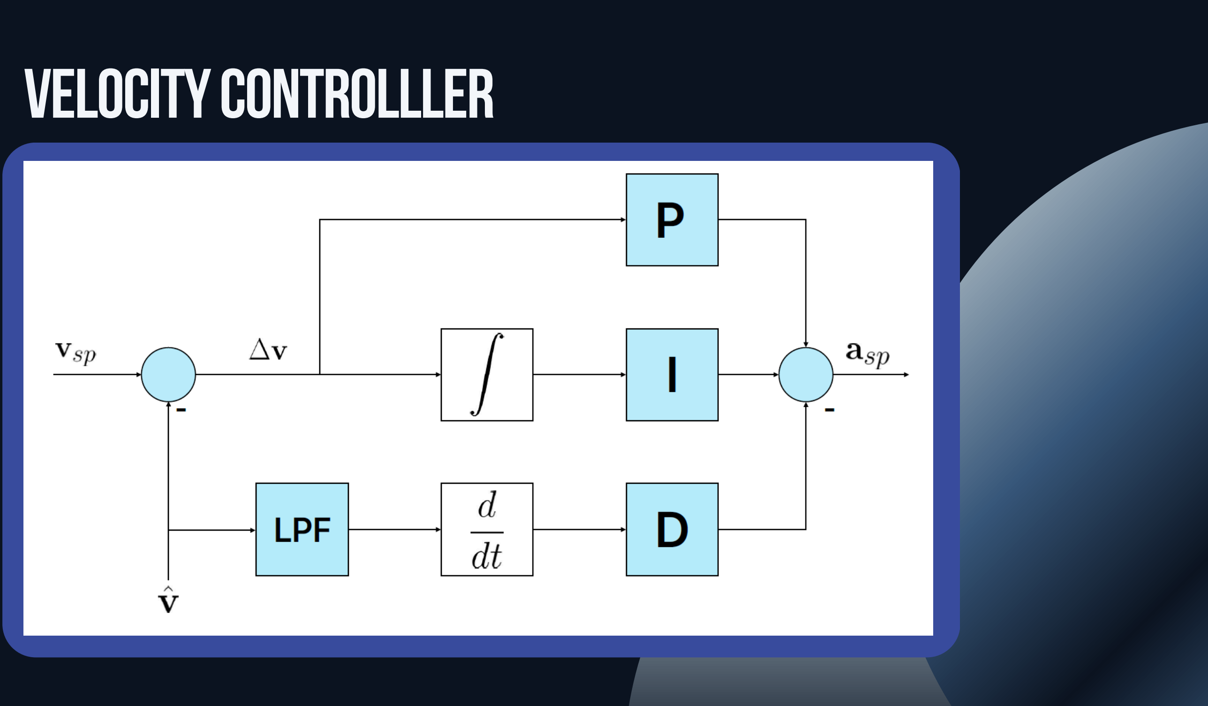
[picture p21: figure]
velocitycontrolller

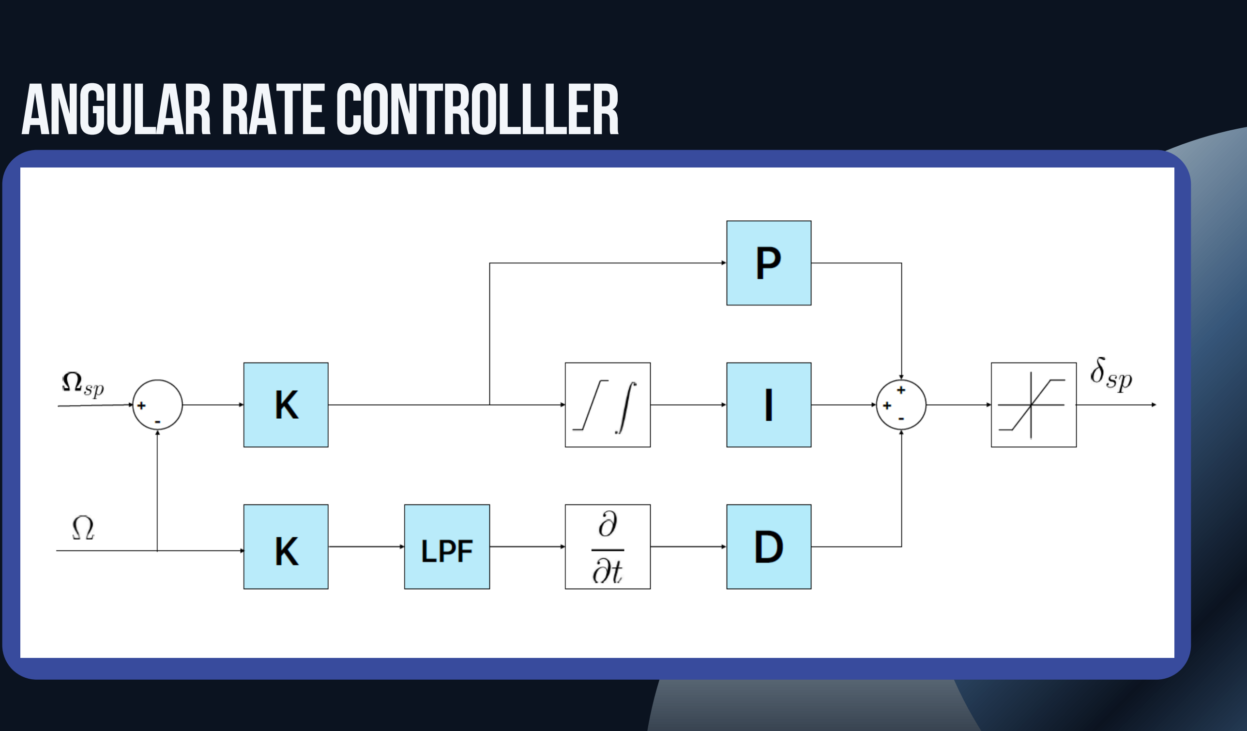
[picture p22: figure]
angular ratecontrolller

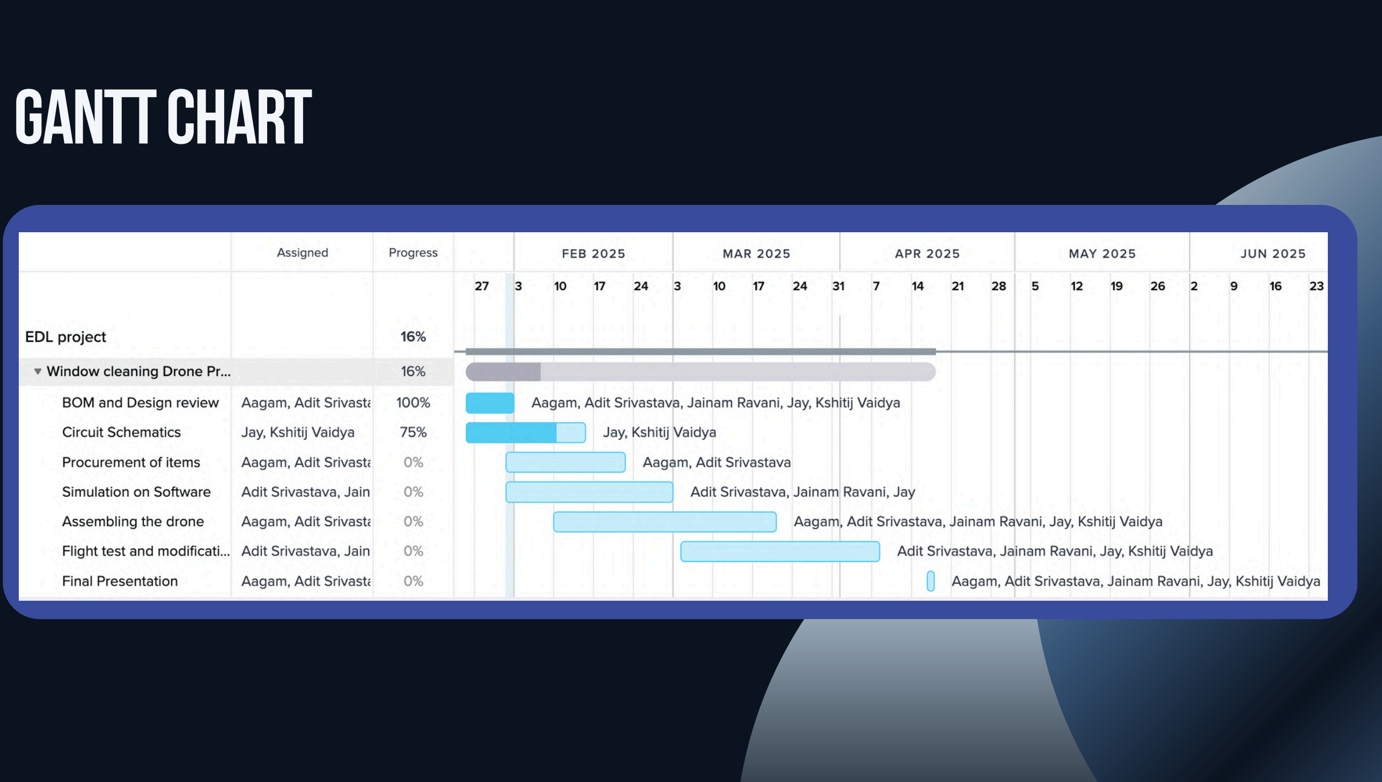
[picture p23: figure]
ganttchart

# Key RisKS andMitigationmeasures

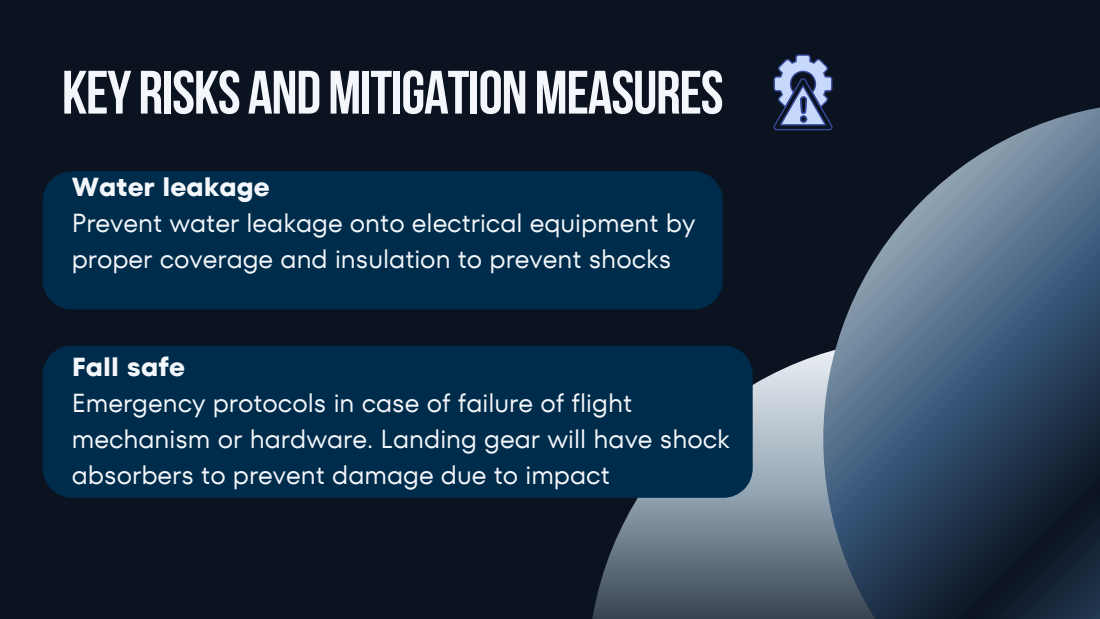
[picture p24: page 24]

Water leakage
Prevent water leakage onto electrical equipment by
proper coverage and insulation to prevent shocks

Fall safe
Emergency protocols in case of failure of flight
mechanism or hardware. Landing gear will have shock
absorbers to prevent damage due to impact

# Deliverables

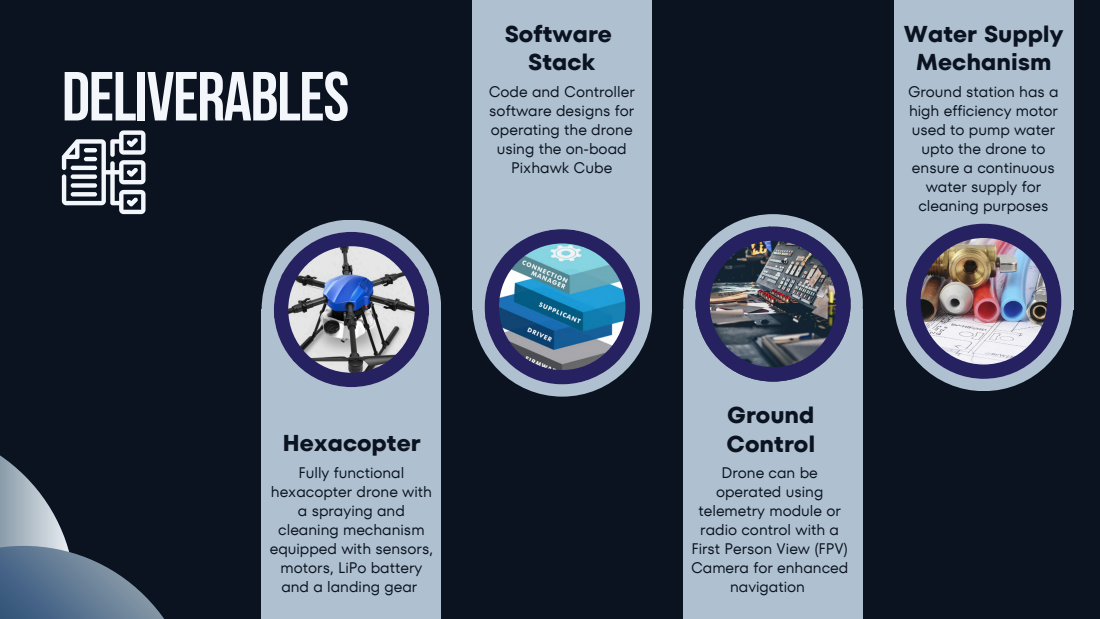
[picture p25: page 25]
Hexacopter; Software Stack; Water Supply Mechanism

Code and Controller
software designs for
operating the drone
using the on-boad
Pixhawk Cube

Ground station has a
high efficiency motor
used to pump water
upto the drone to
ensure a continuous
water supply for
cleaning purposes

Ground
Control
Drone can be
operated using
telemetry module or
radio control with a
First Person View (FPV)
Camera for enhanced
navigation

Fully functional
hexacopter drone with
a spraying and
cleaning mechanism
equipped with sensors,
motors, LiPo battery
and a landing gear

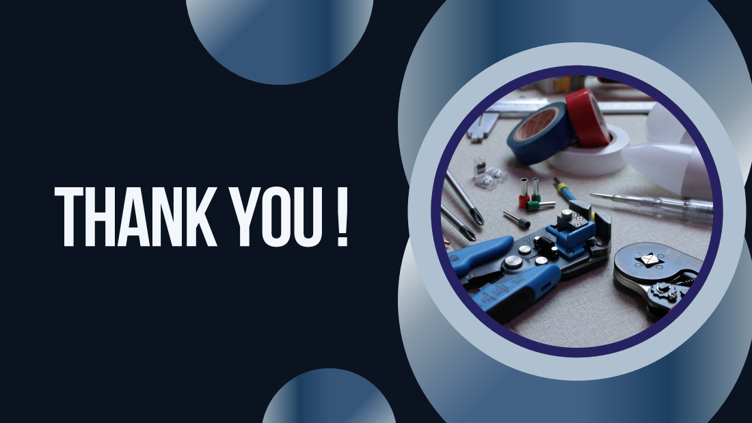
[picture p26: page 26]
Thank you!

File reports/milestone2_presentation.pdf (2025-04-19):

## EE344 :ElectronicDesign Lab

Aagam Shah Jay Mehta Jainam RAvani Kshitij Vaidya AditSrivastava; Window Cleaning Drone

TEAM ID : MON-13

# Challengesin Cleaning High-RiseWindows

Manual Effort and Risks: Cleaning windows of high-rise buildings is labor-intensive and involves significant safety risks for workers

Inefficiency: Traditional methods are time-consuming and require specialized equipment like scaffolding or
suspended platforms

High Costs: Employing skilled labor and safety measures increases operational expenses for building maintenance.

Environmental Challenges: Cleaning in adverse weather conditions or accessing hard-to-reach windows poses additional difficulties.

proposed solution

A specially designed hexacopter drone equipped with | a sprayer and a continuous water supply.

Calculations about power, thrust should be accurate. We have addressed that by performing exhaustive calculations and analysis about all parameters which we will demonstrate in upcoming slides

1.

Plan a minimum deliverable, which now we have decided to keep a fully functional flying drone with a spraying mechanism and a detailed report of calculations,simulations and software stack as a minimum deliverable

2.

Have a more defined project plan, which now we have structured in a better way which we will demonstrate in updated gantt chart

3.

# Feedback FromMilestone1

The battery operated drone gives a very small flight time and is not effectively serving the purpose of the drone. We should look into alternate modes of power supply like tethered connections which power the drone using an SMPS (Explained in detail later). This greatly reduces the cleaning efficiency of the drone

1.

Our thrust and power calculations were assuming a flow rate of 3.5L/min. This is a very high rate of water flow and we can achieve adequate cleaning results at much lower rates of water flow by using more water-efficient spraying mechanisms.

2.

## discussionswith prof.siddharth tallur and ankur sir

Our discussions with Prof. Tallur gave us the following insights which we hope to address and incorporate in our project:

# Project Documentation

Calculations and analysis

A detailed latex report containing all the exhaustive calculations and analysis is posted on OneNote Notebook and a brief summary is presented in this presentation as well

Schematics; Documents containing detailed circuit and

wiring diagrams of various circuit components and whole system have been demonstrated in this presentation and is also posted on Onenote

Simulations and results; The video is also posted on OneNote.

Simulations of the drone and its spraying mechanism are conducted in Gazebo, with the setup and results summarized in this presentation.

Software Architecture

The PX4 autopilot codes have been compiled in a GitHub repository, and a detailed report explaining the software stack is available on OneNote.

# power & mechanical

## Ensure sufficient thrust for stable flight

## Optimize pumping mechanism for efficient water delivery

# Payload and ThrustEstimAtion

Key Components in terms of weight:
Chassis - 720g
Water Column - 712g
Battery - 260g
BLDC Motors - 25*6 = 150g
12V DC Motor - 50g
Total Payload = 2.385 kg

Total Thrust required = 23.4N
Thrust per Motor = 3.9N

# RPMEstimAtion

Diameter = 9 inches

The relation between Thrust, RPM, Pitch and Diameter of a
Propeller is given by:

For our propellers: Pitch = 4.7 inches

RPM Required = 6652 RPM

KV Rating for a Motor is defined as the Voltage required per 1000 RPM of Motor Speed.

## Using KV Rating of Motors

For 6652 RPM, Voltage required = 6.652V
Average Current drawn = 7A

# Power Drawn = 46.5 W

# Motor Power EstimAtion

Using Datasheet of Motors

The datasheet suggests a RPM of 6600 RPM for
9x5 Propellers requires:
Power Drawn = 52 W

We will be using this value for further analysis
Total Power drawn = 52*6 = 312 W

## The Power for each component is as follows:

# TotalPower EstimAtion


Battery Capacity = 3300 mAh
Voltage = 14.8 V (4S Battery)

Battery Life = 8.23 mins

# BatteryLife vsPerformanceTrade-off

The drone’s 8.23-minute battery life is sufficient for demonstrations, but extending it poses challenges. A higher capacity battery increases weight, reducing the thrust-to-weight ratio, while better motors and propellers raise power consumption. Achieving the required 4-hour battery life is impractical for this size, as a larger drone would significantly increase costs. A tethered power supply removes battery constraints but limits range, adds complexity, and poses safety risks. Thus, a trade-off is necessary between battery life, performance, and feasibility.

We have also planned for an alternate method for powering the drone to improve the flight time of the drone and also eliminate the need for rechargeable onboard batteries

SMPS is an AC-DC Power Source that operates at a high efficiency and with minimal heat dissipation.

A Switching Mode Power Supply stationed on the ground
can be used to power the drone via a tethered connection. This improves the flight time because of a continuous power supply for the drone

Power Rating | 750 W
Voltage | 12 V
Current Rating | 62.5 A

The SMPS selected for this method is UHP-750-12 by Meanwell.

These specifications cover the steady state and the take off operation.

Problemswith smps; need to be as stable as possible.; drone and the onboard motors.; SAFETY HAZARD; increasein payload

Using an SMPS and the tethered connection adds the potential risk of a hanging cable carrying a high current thus the flight operations of the drone

Also, the wire adds a significant weight to the drone increasing the payload requirements of the

Our initial proposal was to supply water using a ground-stationed motor that would pump water up to the drone at a constant rate. This ensures a continuous and high rate of water supply to the drone.

Upon further discussion, the water flow rate and motor specifications decided by us were more than the requirements of the projects and so we have to look into alternate options with lesser water supply capacities.

The tank can be refilled as and when required.
For this to be a viable solution, however, the spraying and cleaning mechanisms used by the drone must be very efficient in their water usage to ensure that the water capacity of the drone is not a limiting factor in effective and consistent cleaning results.

### Small 0.5-1L On-board Tank

## Proposal

Using a tank removes the hazard of adding a water pipe and also eliminates the need for a ground-stationed motor. This however adds a payload of the tank weight and the water in holds on the drone. Thus the capacity of the tank must be chosen appropriately to ensure that it does not add excessive thrust strain on the motors while allowing for an appropriate quantity of water to clean the surfaces properly. Adding a water tank also requires careful consideration of the centre of gravity of the drone and carefully managing the weight distribution of the drone to ensure that it can operate stably. We can also have multiple tanks and a simple fitting mechanism that makes the refilling and replacement of the water tank faster to improve the overall efficiency of the drone.

# Max Thrust Analysis

9660 RPM | 49.35 N

Corresponding
max thrust per
motor

Max Total Thrust

8.225 N

Thrust to weight
ratio

2.11

# HorizontalthrustEstimAtion

12V DC Motor can provide a maximum pressure of 4.8 bar
We assume pressure difference of 2 bar since we don't want
the motor to run at maximum capacity at all times

Using the above formula, we get Exit Velocity around 20 m/s
Horizontal Thrust = Mass Flow x Exit Velocity
Horizontal Thrust = 1.166 N

# ground pump Analysis

## 0.0583 kg/s

Ground Pump
Power Needed

Mass Flow

250-300 W

Upward Thurst
Required =
Mass Flow* Velocity
0.0477 N

## 71.26 mm^2

Area of pipe

0.818 m/s

Velocity

# vector diagramof allthrusts

The calculated tilt angle
of the drone is 2.38
degrees. This angle is well within achievable limits
for the drone.
The tilt is needed to
counter the horizontal
thrust.

# vehicular dynamics

# hex-rotor dynamics

Body frame, {B}:; some Notations:

World (inertial) frame, {W} :

COM position in {W}:

Roll-Pitch-Yaw in {B}:

Angular rates in {B}:

r

o

# translational dynamics


Including gravity, we get:

Here R is as defined in previous slide and g = acceleration due
to gravity

# rotational dynamics

Relation of (p, q, r) with rate of change of roll-
pitch-yaw angles:

# rotational dynamics

## Moments and Euler’s Equations:

Inertia in {B}:

: Torque about z_B from rotor i

Each rotor exerts a thrust F_i at some position r_i
in x_B - y_B plane

Euler’s rigid-body equations:

# propeller thrust andmotor dynamics

where omega_i is the rotor speed and k_F, k_M are empirically
determined constants.

Half the rotors spin CW and other half spin CCW so sum of their
torques can cancel in hover.

where omega_cmd,i is the commanded speed and k_m is a
motor constant

Many Hex-rotor and Quad-rotor controllers assume the vehicle remains stable during hover. Under small angles, one can linearise the dynamics. Hence we can break it into two control loops:
Outer (position) loop: Runs at a lower frequency and uses position/velocity feedback to set desired roll, pitch, thrust

1.

Inner (attitude) loop: Runs at a higher frequency, uses onboard Gyros/Accelerometers to stabilise roll, pitch and yaw.

2.

# attitudecontrol

: Total Thrust

Assumptions near hover:

PD laws for each axis:

: Moments about body axes

# mixer equation

Representative M matrix for a particular Hex-rotor layout

b = k_F (force constant), d = k_M (moment constant), l = vehicle
center to rotor distance.
Inverting or pseudo-inverting M determine omega_i for particular u

# position control

Thus:

We control (x, y, z) in this loop. Near hover, ignoring drag
we have:

These commands are fed into the inner attitude controller,
ensuring the vehicle follows the desired trajectory in position.

# software ArChitecture

# PX4Softwarestack

PX4 Autopilot is widely used for
flight control due to its modular
architecture, compatibility with
various flight controllers, and
intuitive uORB communication bus.
For our implementation, minimal
changes will be made to the core
control stack since its operation
has already been validated in
simulation.
If a custom controller is required,
an alternative pipeline has also
been proposed.

R

O

S

P

X

4 In

t

e

r

f

a

c

e

# gazebo simulation

Component | Dimsensions | Mass | MoI (Ix) | MoI (Iy) | MoI (Iz)
Chassis | 0.67 x 0.67 x 0.15 | 0.997 | 0.039 | 0.039 | 0.075
Camera | 0.01 x 0.01 x 0.01 | 0.011 | 1.83e-7 | 1.83e-7 | 1.83e-7
Landing Legs | 0.01 x 0.03 (r x h) | 0.1 | 7.54e-4 | 7.54e-4 | 7.45e-3
Rotors | 0.128 x 0.005 (r x h) | 0.024 | 9.83e-5 | 9.83e-5 | 1.97e-4
Nozzle | 0.05 x 0.12 (r x h) | 0.05 | 0.07 | 0.07 | 0.07

# inertialparameters

Parameters | Value
Time Constant (s) | 0.0125
Max Speed (rad/s) | 1240
Max Speed (RPM) | 11840
Motor Constant (N · s^2/rad^2) | 8.038e-6
Moment Constant (N · m · s^2/rad^2) | 9.55e-3
Rotor Drag Constant | 0.09637
Rolling Moment Coefficient | 1e-6

# motor parameters

Simulator | Gazebo classic
Drone Model | Typhoon H480
Autopilot | PX4 v1.14
Middleware | ROS2 with MicroXRCE bridge

## Objective

Take off the drone and maintain a constant altitude for 10s.
To start spraying water in the specified direction.
To ascend upwards by some distance while spraying water and then stabilizing at its original altitude

For spraying mechanism, we have tried to simulate weight of water column by applying forces as shown

## Note

The simulation results obtained at the current takeoff altitude can be extrapolated to any other altitude since the air density and pressure is uniform throughout the simulation

Simulation Video

# Simulation Results

# Position Plot


The drone takes off at T=40s and attains a
stable altitude thereafter.
At T=47s, the spraying mechanism is
enabled which leads to a recoil force of 10N
in the Y direction and an additional
downward force of 11N in the Z direction.
This subsequently leads to a perturbation of
around 0.3m in the Y direction and a drop in
altitude of around 0.2m.
The drone then eventually stabilises at its
nominal position.

# Simulation Results

### Settling time = 5s


# Y coordinate plot

# Z coordinate plot

# Simulation Results

Attitude plot

The drone maintains a stable roll
and yaw angle throughout the
mission.
The pitch angle increases slightly
after T=47s to counter the recoil
force and the additional weight of
the water column.

# Pitch plot

The drone stabilises with a slight tilt in orientation.
The drone maintains this orientation throughout the spraying process. The tilt can be described by a Pitch angle which is around 20 degrees.

Time Duration; Control Value; RPM; 47s onwards; Simulation Results; Motor control plot; 11840 RPM.

The Control Value is the fraction of the maximum speed of the motor of the model which is 1240 rad/s or


# circuit diagrams

power distribution board (PDB); The Chassis comes with an in-built PDB, which we can use to route power to each BLDC Motor using an ESC. The Diaphragm Motor is also powered using this. The PixHawk and RPi are also powered through the PDB with a BEC to step down voltage.

pixhawk connections; The PixHawk Cube is the centerpiece of the drone which will control the flight as well as communications. The RC Rx, Telemetry Modules, ESCs for Motors, RPi are all connected to the Cube using appropriate connections.

Raspberrypi-4connections; The Raspberry Pi-4 is essentially on-board to serve as a video broadcasting method. The NoIR Camera is connected to the RPi. The camera feed will be relayed to the ground station using WiFi.

# testing plan

# preliminarytesting

# Power and

SITL Testing; HITL Testing

Flight Analysis
Analyze the log files
generated by the
simulator to compare
the estimated power
and state values with
the simulated values.

Simulate the drone
operation on Gazebo
Simulator using the
actual flight controller
for a more accurate
representation of real-
world behavior.

Simulator using model
parameters of the
hardware drone.

Evaluate it’s current and voltage; reaches the desired value.; SMPS; For various values of the PWM input and power input from the SMPS evaluate the motor speed and estimate the thrust generated; Using a ground pump, note the speed and volume of water dispensed; Pumping Mechanism; Nozzle Control; Using the pumping mechanism, ensure that the servo controlled valve operates as desired.; ESC+BLDC motors; Communi- cation; Test the RC, Telemetry and Video Streaming modules seperately

output and adjust the regulation till it

Ensure that the drone accepts high level setpoints from the GCS and smoothly navigates to the desired position.

On enabling the spraying mechanism, ensure that the drone suffers minimal perturbation and eventually stabilizes

Test the system on an unclean window and ensure that the drone can effectively clean a window pane

Ensure that the drone can maintain a stable altitude of 10m for the flight duration with reliable communication with GCS Altitude Hold

## Waypoint Travesal

## Recoil Tolerance

## Effectiveness of cleaning

Thank you!

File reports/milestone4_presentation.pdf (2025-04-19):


# Drone Alone

Aagam Shah (22B1201) | Adit Srivastava (22B1269) | Jainam Ravani (22B1242) | Jay Mehta (22B1281) | Kshitij Vaidya (22B1829)

A hexacopter drone with a high payload capacity capable of cleaning walls and windows which can be employed by buildings and organisations to clean inaccessible areas of buildings without the risk of safety due to manual labour.

# Status Report

Key Specs Proposed | Status | Remarks
2kg Payload Capacity | Complete
Cleaning Mechanism – Spray Nozzle and Wiping Brush | Partially Complete | Wiping brush couldn’t be done since it would result in imbalance in weight and result in an unstable vehicle
Operating Range – 100m | Complete
FPV Navigation | Complete
4hr Battery Life | Partially Complete | This would require a very high payload due to battery mass or a ground SMPS which would result in high power losses. Current Battery Life ~20 mins
Stable operation under windy conditions and efficient handling of recoil | Complete

# Mechanical Assembly


This shows the drone from various
angles wherein the placement of
the tank, the outlet pipe and the
water pump can be seen clearly.
The ESCs have been placed on the
arms of the drone. No pipes or
wires are left dangling to prevent
entanglement with propellers.

This is the layout of the bottom plate of the drone where the main wiring of the drone, which distributes power to all components, is placed.
The key focus is on modularity and ease of usage by adding connectors at almost all junctions. This makes it easy to change components without having to solder and desolder every time.


This shows the placements of all the components on the top plate of the drone. All the wires shown here fit inside the canopy and hence are safe from entanglement in the propellers. The PixHawk and GPS need to be placed in the centre of the drone for proper control and the battery is in the centre to prevent weight imbalance.

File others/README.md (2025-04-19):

# Others

This is a directory that includes some additional information about our project. We also include a User Manual that contains vital information about operating our drone. We strongly encourage going through the Manual to operate our drone safely and in the proper intended manner.

This directory also has a subdirectory `simulation` which includes some discussions about our simulation results. We used Gazebo to simulate our drone and study its response to the application of an external force. This was done to understand the ability of the drone and the flight controller to handle the recoil caused by the water spraying mechanism. 

## Directory Structure

```bash
.
├── simulation
│   ├── simulation.py
|   └── README.md
└── user_manual
    ├── user_manual.pdf
    └── README.md
```

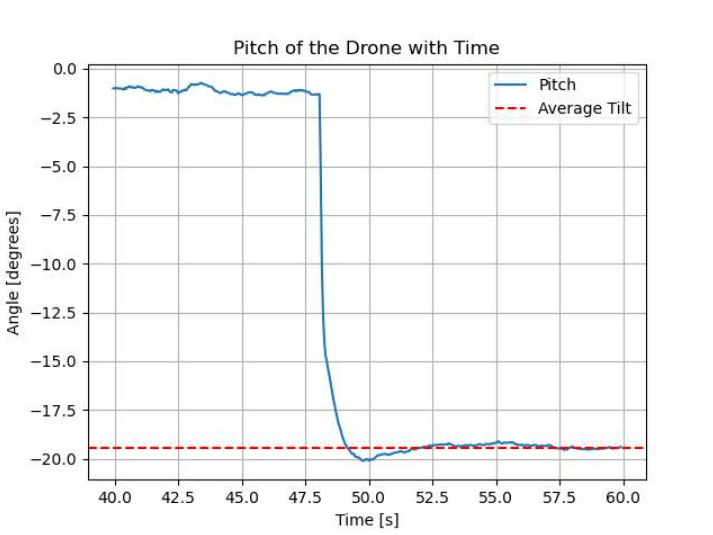
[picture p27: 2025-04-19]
others/simulation/pitch.png

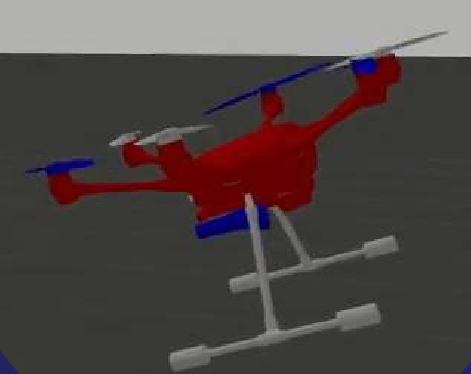
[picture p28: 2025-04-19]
others/simulation/drone.png

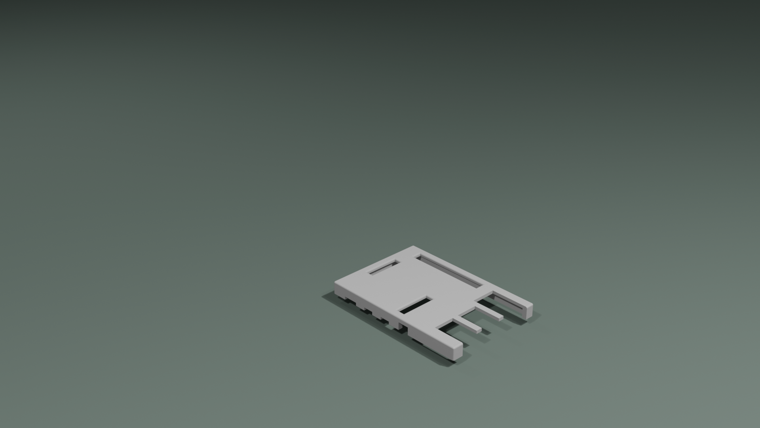
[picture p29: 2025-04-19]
3d_models/Raspberry Pi Casing Top/rpi_casing_top.PNG

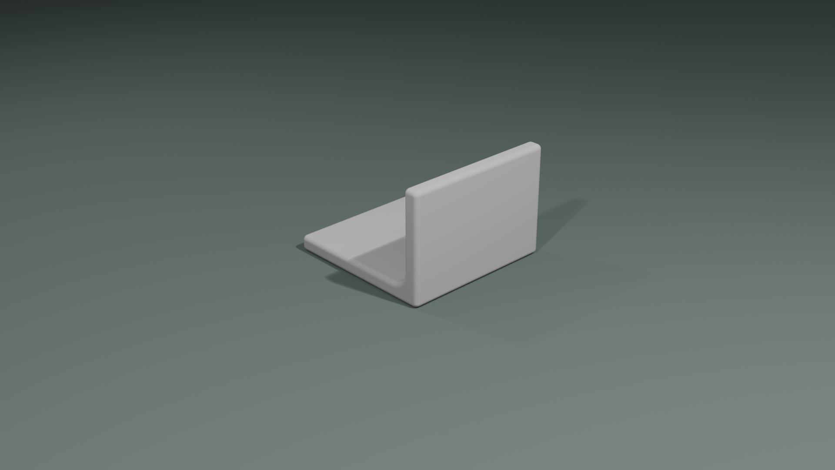
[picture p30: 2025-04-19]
3d_models/Clamp for Diaphragm Pump/diaphragm_pump_clamp.PNG

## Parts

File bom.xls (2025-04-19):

Project Title: Glass/Wall Pane Cleaning Drone
Group ID: MON-13
Name of the Group Member/s: Kshitij Vaidya, Jay Mehta, Jainam Ravani, Adit Srivastava, Aagam Shah
Contact details of the Group Member responsible for BOM: Kshitij Vaidya (9137589406, 22b1829@iitb.ac.in) Jainam Ravani (9326641433, 22b1242@iitb.ac.in)
BOM
Sr.No | Description | Part name and number | WEL Component stock Location-ID | Vendor | Link (Vendor online website) | Required Qty + Spare | Cost per each item | Total Cost
1 | Hardware Main Body | S550 Hexacopter Frame (Carbon Fiber) | NA | Robu.in | https://robu.in/product/s550-hexacopter-frame/ | 1 | 4499 | 4499
2 | Propulsion and Flight System | A2212 Brushless DC Motors (1000KV) with SimonK 30A ESC | NA | Robu.in | https://robu.in/product/a2212-13t-1000kv-brushless-motor-outrunner-30a-esc/ | 6 | 660.33 | 3961.98
3 | Flight Controller | Pixhawk Cube | NA | Robu.in | https://robu.in/product/hex-pixhawk-cube-flight-controller-autopilot/ | 1 | 33733 | 33733
4 | Main Power Supply | 3300mAh 4S LiPo Battery (Bonka) | NA | Robu.in | https://robu.in/product/bonka-14-8v-3300mah-25c-4s-lithium-polymer-battery-pack/ | 2 | 2299 | 4598
5 | Hardware Components for Flight | Propeller Blades - Orange Propellers 9047 | NA | Robu.in | https://robu.in/product/orange-hd-propellers-90479x4-7-carbon-nylon-dji-1cw1ccw-1pair-black-2/ | 6 | 299 | 1794
6 | Water Carrying system | 1/2'' Flexible Pipe (60cm) | NA | https://www.amazon.in/ | https://www.amazon.in/AQUALIQUID-RO-Water-Purifier-Meter/dp/B08KZR1684 | 1 | 343 | 343
7 | Pumping Mechanism | 12V DC Motor | NA | Robu.in | https://robu.in/product/550-diaphragm-pump-12v-water-pump-for-water-spray-fish-tank-reflux-pump/ | 1 | 374 | 374
8 | Communication system | Telemetry Sik Module | NA | Robu.in | https://robu.in/product/holybro-sik-telemetry-radio-v3-100-mw-433-mhz/ | 1 | 6499 | 6499
9 | Camera for FPV | RASPBERRY-PI Daughter Board, Raspberry Pi NoIR Camera Board, Version 2, Sony IMX219 8-Megapixel Sensor | 2K.BOX-9.130 |  |  | 1 |  | 0
10 | Onboard Computing Module | RASPBERRY-PI SBC, Raspberry Pi4 B 8GB, BCM2711, ARM Cortex-A72, 8GB RAM, MicroSD, Linux, Wifi, 2x micro HDMI | 2K.BOX-9.131 |  |  | 1 |  | 0
11 | RC Module | Radiomaster TX16S MKII HALL V4.0 ELRS Radio with RP1 ExpressLRS 2.4ghz Nano Receiver | NA | Borrowed from UMIC | https://robu.in/product/radiomaster-tx16s-mkii-hall-v4-0-elrs-radio-controller/ | 1 | 17169 | 17169
12 | Power Distribution System | BEC 5V 5A | NA | Robu.in | https://robu.in/product/2-13s-5v-5a-bec-for-quadcopter-drone/ | 3 | 866 | 2598
13 | Connector Arm | 30 cm PVC pipe | NA |  | Local Hardware Shop | 1 | 30 | 30
14 | Assembly of Pipes | Pipe Clips | NA |  | Local Hardware Shop | 3 | 10 | 30
15 | Spraying Mechanism | Nozzle | NA |  | Local Hardware Shop | 1 | 299 | 299
16 | Power Distribution System | Single Sided Copper Clad | NA |  | Procured from PCB lab | 2 |  | 0
17 | Electrical Assembly tools | XT60 connectors pairs | NA |  | Local Hardware Shop | 7 | 50 | 350
18 | RC Module battery | 2200mAh 2S LiPo Battery (Bonka) | NA | Borrowed from UMIC | https://robu.in/product/orange-2200mah-2s-45c-lithium-polymer-battery-pack-lipo/?gad_source=1 |  |  | 0
19 | Motor Driver | L298N Motor Driver Module | NA | Team Member's Personal | https://robu.in/product/l298n-2a-based-motor-driver-module-good-quality/?gad_source=1 | 1 | 101 | 101
20 | GPS Module for position estimate | 32db High Gain Cirocomm 5cm Active GPS Antenna | NA | Borrowed from UMIC | https://www.amazon.com/CIROCOMM-Antenna-Ceramic-25x25x2mm-Geekstory/dp/B078Y2WNY6 | 1 | 516 | 516
21 | Mechanical Support for Pump | 3D printed Clamp | NA |  | 3D printed from UMIC lab | 1 |  | 0
22 | Water Storage System | 3D printed Water Tank and Cap | NA |  | 3D printed from UMIC lab | 1 |  | 0
23 | Mechanical protection for Drone | 3D printed Canopy | NA |  | 3D printed from UMIC lab | 1 |  | 0
24 | Mechanical protection for Rpi | 3D printed Casing | NA |  | 3D printed from UMIC lab | 1 |  | 0
25 | Mechanical protection for Flight Controller | 3D printed Pixhawk Casing | NA |  | 3D printed from UMIC lab | 1 |  | 0
26 | Mechanical assembly tools | 3mm Spacers (length 2cm) | NA |  | Local Hardware Shop | 2 | 12 | 24
27 | Mechanical assembly tools | 3mm Nuts and Bolts (25 mm length) | NA |  | Local Hardware Shop | 12 | 2 | 24
28 | Mechanical assembly tools | 2mm Nuts and Bolts (25 mm length) | NA |  | Local Hardware Shop | 2 | 3 | 6
29 | Electrical Assembly tools | Jumper Wires (FtoF,MtoM,MtoF) | NA | Team Member's Personal |  | 20 | 1 | 20
 |  |  |  |  |  |  | Total | 76968.98
Equipments and Additional Accessories
1 | Glue Gun
2 | Soldering Iron
3 | M-seal
4 | Angle Grinder
5 | Heat shrinks
6 | Hexkey
7 | Screw Drivers
8 | Insulation Tapes
9 | Double Sided Tape
10 | FeviKwik
11 | LiPo Battery Charger
12 | Zip-Ties

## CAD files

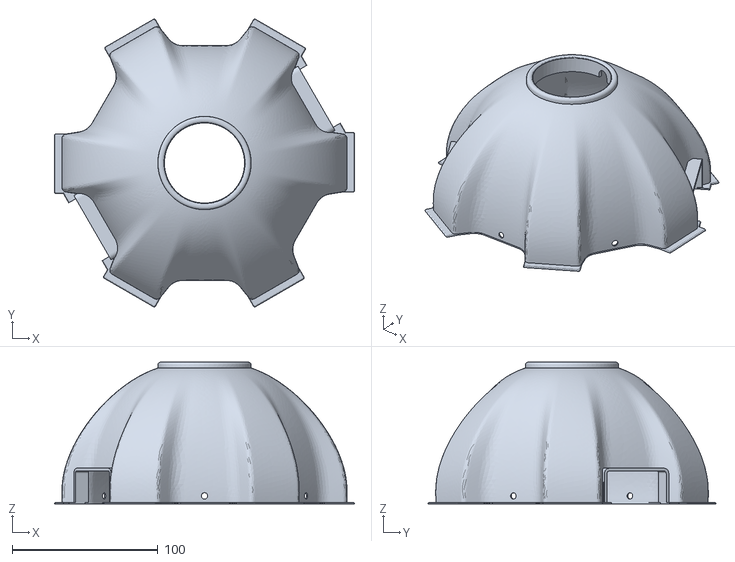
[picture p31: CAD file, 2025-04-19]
3d_models/Canopy/canopy.stl
205.9 x 197.6 x 97.3

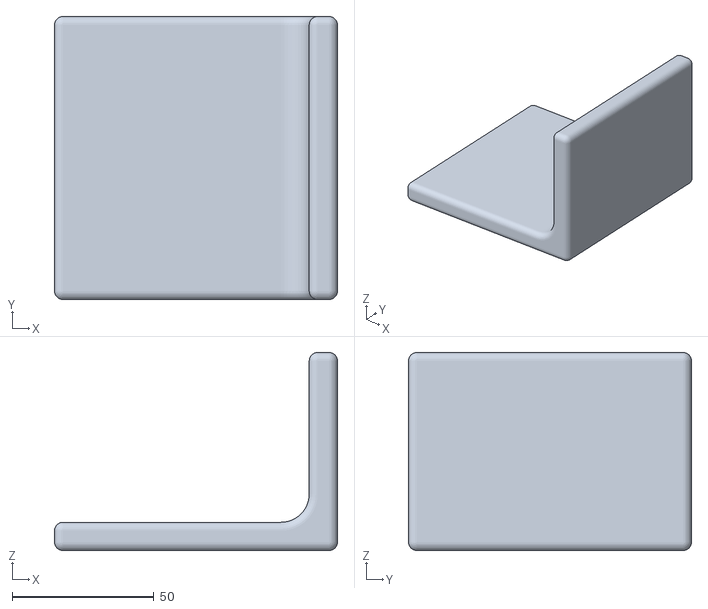
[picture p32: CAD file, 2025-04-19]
3d_models/Clamp for Diaphragm Pump/diaphragm_pump_clamp.stl
100.0 x 100.0 x 70.0

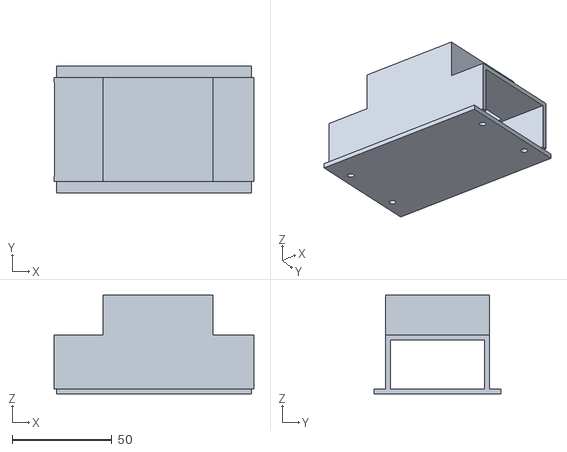
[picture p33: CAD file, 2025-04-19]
3d_models/PixHawk Casing/pixhawk_casing.stl
100.4 x 64.0 x 49.5

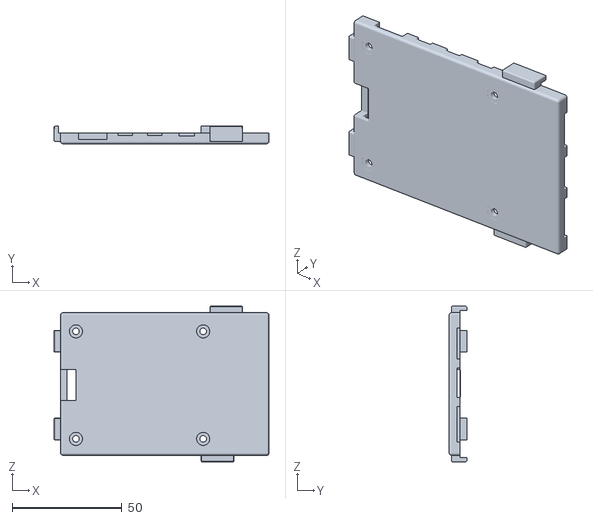
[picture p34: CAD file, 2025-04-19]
3d_models/Raspberry Pi Casing Bottom/rpi_casing_bottom.stl
98.0 x 8.00 x 71.0

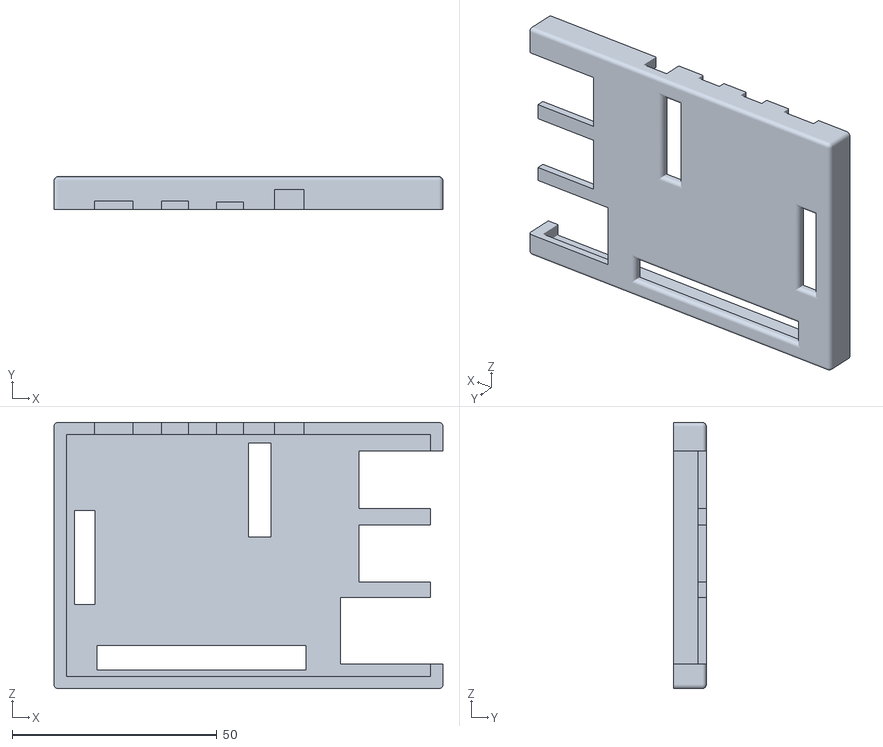
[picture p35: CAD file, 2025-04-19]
3d_models/Raspberry Pi Casing Top/rpi_casing_top.stl
95.0 x 8.00 x 65.0

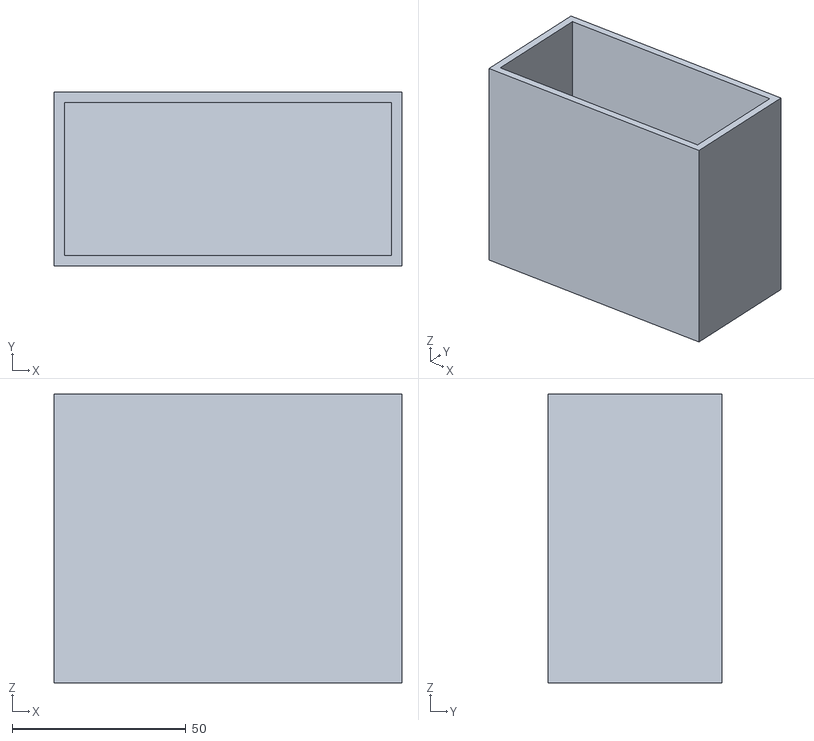
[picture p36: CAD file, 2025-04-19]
3d_models/Tank Container/tank_container.stl
100.0 x 50.0 x 83.0

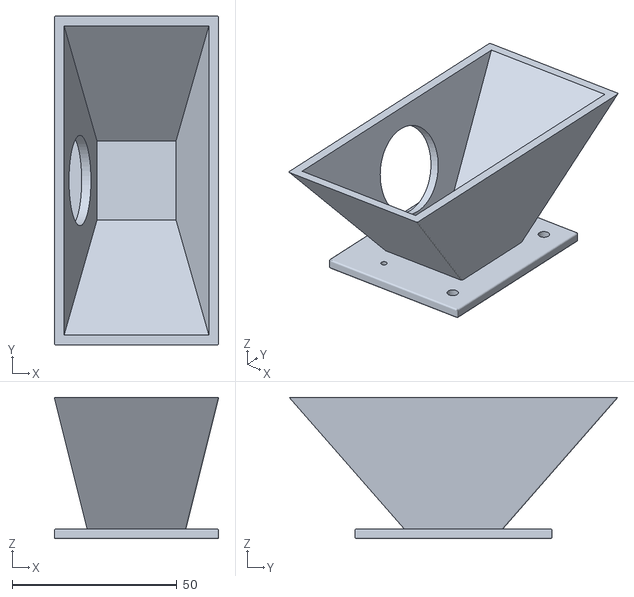
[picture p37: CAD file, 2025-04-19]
3d_models/Tank Cover/tank_cover.stl
50.0 x 100.0 x 43.0

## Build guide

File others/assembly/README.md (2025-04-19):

## Contents
- `arm_attachments.jpg`
- `back_view.jpg`
- `centering_of_pixhawk_battery.jpg`
- `close_up_motor_clamp.jpg`
- `front_view.jpg`
- `isometric_view.jpg`
- `left_side_view.jpg`
- `motor_clamp.jpg`
- `pixhawk_assembly.jpg`
- `pump_tank_assembly.jpg`
- `README.md`
- `right_side_view.jpg`
- `top_view_without_canopy.jpg`
- `top_view.jpg`

## Description

1. `arm_attachments.jpg`: Photograph showing the attachments between the Arm and the two Plates
2. `back_view.jpg`: Back view of the drone showing the tank attachments 
3. `centering_of_pixhawk_battery.jpg`: Centering of the Pixhawk and Battery to maintain balance
4. `close_up_motor_clamp.jpg`: Close up shot of the motor clamp 
5. `front_view.jpg`: Front view of the drone
6. `isometric_view.jpg`: Isometric view of the drone
7. `left_side_view.jpg`: Left side view of the drone
8. `motor_clamp.jpg`: Photograph showing the motor clamp position
9. `pixhawk_assembly.jpg`: Photo showing the connections of the Pixhawk
10. `pump_tank_assembly.jpg`: Photo showing the tank and motor aseembly and how they are connected
11. `right_side_view.jpg`: Right side view of the drone showing relative position of tank and motor with respect to the bottom plate
12. `top_view_without_canopy.jpg`: Top view of the drone without the canopy
13. `top_view.jpg`: Top view of the drone with the canopy

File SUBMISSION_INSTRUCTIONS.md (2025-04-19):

# Project Documentation and Submission Guide

This document serves as a comprehensive guide for your project submission. By following the instructions below, you will ensure that the project is properly organized, documented, and easy for others (such as professors or staff members) to understand and replicate.

Your entire project is graded based on this submission and so please adhere to this properly. Stick to the hard deadline given and NO EXTENSIONS WILL BE GRANTED AT ANY POINT IF IT IS NOT COMPLETED.

## Project Overview

### Project Name: P08 - Wall/Glass Pane Cleaning Drone
### Team Number: MON-13
### Team Members:
- Aagam Shah
- Adit Srivastava
- Jainam Ravani
- Jay Mehta
- Kshitij Vaidya

### Problem Statement and Solution:

Provide a description about the project and what you've learnt and achieved in this.

Make sure to add all the below properly as given and if it's applicable.

## 1. Source Code

All source code files should be organized under the `/src` directory. If your project involves multiple microcontrollers or processors, create respective subfolders for each and provide clear descriptions about their purpose and functionality. Every subfolder should have a README.MD file which should explain the purpose of the code and all the commands used.

### Folder Structure:
```plaintext
/Project-Root 
├── /src # Source code folder (Add your source files here) 
  ├── /microcontroller1 # Code for Microcontroller 1 
    ├── file1.c # General source file 
    ├── file2.c
  ├── /microcontroller2 # Code for Microcontroller 2 (if applicable) 
    ├── file1.c # General source file 
    ├── file2.c
```

### Guidelines for Organizing Code:
1. **Microcontroller-specific code**:  
   If your project involves multiple microcontrollers, create a folder for each one under `/src`. Provide the following details:
   
   - **Folder Name**: Name it according to the microcontroller, e.g., `Microcontroller1`, `Microcontroller2`.
   - **Description**: A brief description of what each microcontroller’s source code does and its role in the project in a README.md file.

Example:
```plaintext
/src 
  ├── /<microcontroller_name1> 
    ├── <relevant_sources.c>  # All source codes
    ├── README.md  # Clear Documentation on the usage of board along with the commands and steps performed
  ├── /<microcontroller_name2> 
    ├── <relevant_sources.c>  # All source codes
    ├── README.md  # Clear Documentation on the usage of board along with the commands and steps performed
......
......
```

2. **Running the Application**:
- If your project is based on microcontroller code, provide detailed instructions on how to upload and run the code on the microcontroller. This should include:
  - The microcontroller model (e.g. STM32, RPi Pico).
  - The Integrated Development Environment (IDE) used for programming (e.g., STM32CubeIDE, VSCode, Thonny IDE).
  - Steps for compiling and uploading the code to the device.
  - Example command to upload (if applicable).

3. **Code Comments**:
- Every source file should be properly commented to describe the purpose and function of each section of code.
- If you have made modifications to an existing code template or framework, comment clearly with your team name and indicate what changes were made.

---

## 2. PCB Design (If Applicable)

If your project involves designing a printed circuit board (PCB), provide the design files in the `/pcb` folder. If you have multiple PCBs, create separate subfolders for each design. Mention the tool used to design the PCB. (KiCAD, Altium, EAGLE). Include the picture of your final PCB Layout (With visibility of all the layers) under the `/pcb/<PCB_X>/pictures` folder with the layer names along with the picture of the Printed PCB which you've obtained.

### Folder Structure:
```plaintext
/Project-Root 
├── /pcb 
  ├── /PCB1 # First PCB Design 
    ├── design.kicad_pcb # PCB Design in KiCAD format 
    ├── schematic.sch # KiCAD Schematic 
  ├── /PCB2 # Second PCB Design (if applicable) 
    ├── design.sch # PCB Schematic
    ├── design.kicad_pcb # PCB Design in KiCAD format 
```
Include all relevant design files such as schematics, board layouts, custom schematic and footprints used and imported if applicable.

---

## 3. 3D Models / Laser Cuts

If your project includes 3D models or components that require laser cutting, place these files in the `/3d_models` directory. Create separate subfolders for different models and provide a description of the design process and tools used.

### Folder Structure:
```plaintext
/Project-Root 
├── /3d_models 
  ├── /component1 # 3D Model for Component 1 
    ├── model.stl # 3D model file 
    ├── picture.png # Rendered image of the 3D model 
  ├── /component2 
    ├── model.obj 
    ├── picture.jpg
```
Make sure to also include images (e.g., PNG, JPG) of the components that were laser cut or 3D printed.

---

## 4. Bill of Materials (BOM)

Provide a complete Bill of Materials (BOM) listing all the hardware components used in your project. This should include both parts obtained from the lab and parts ordered from external vendors or purchased locally.

### Folder Structure:
```plaintext
/Project-Root 
├── bom.xls # Excel sheet listing components
```

### BOM Details:
The `bom.xls` file should include the following columns:
- **Component Name**
- **Type** (3D Model / Modules / IC / Consumables / Sensors & Actuators)
- **Quantity**
- **Part Number** (if applicable)
- **Supplier/Manufacturer/Vendor/Purchased Place**
- **Cost**
- **Description**

---

## 5. Reports and Presentations

Provide your project presentation and reports in either `.pptx`, `.ppt`, or `.pdf` format. This should include a brief overview of your project, objectives, design process, results, and conclusions. This should include all the milestone submission presentations.

### Folder Structure:
```plaintext
/Project-Root
  ├── /reports 
    ├── presentation.pptx # PowerPoint presentation file
    ├── milestone_reports.pdf # Milestone Reports in PDF file
```

## 6. Other Documents

Provide the wiring diagram of your components, attach pictures of your final project on how did you assemble the design. Place these files in the `/others` directory.
Any other important information regarding your project if it doesn't fit into any of the above categories, add it into this subfolder along with a proper README.md file to explain the same.

## Final Notes:
- **Documentation**: Ensure that all your files are well-documented. This includes commenting your code, describing your designs, and providing detailed instructions in your README file.

By following these instructions, your project will be well-organized, easy to understand, and reproducible by others, including professors or staff members who might need to verify or recreate your project in the future.

Thank you, and best of luck with your project!

---

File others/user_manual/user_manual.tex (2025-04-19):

\documentclass[12pt,a4paper]{article}
\usepackage[utf8]{inputenc}
\usepackage{geometry}
\geometry{margin=1in}
\usepackage{lipsum} % For sample text, can be removed

\begin{document}

\title{Wall/Glass Pane Cleaning Drone}
\author{User Manual}
\date{\today}

\maketitle

\section{Introduction}
This manual covers the essential steps for operating the drone. Before proceeding, ensure that all assembly is carried out correctly as per the existing GitHub repository instructions. 

\section{Starting the Drone}
\begin{enumerate}
    \item \textbf{Connect the data cable} to the Pixhawk Cube flight controller.
    \item \textbf{Connect the battery} to the rest of the circuit. This action powers all ESCs (Electronic Speed Controllers), and you should hear a short tune with three beeps indicating that all ESCs are successfully powered on.
    \item \textbf{Connect the telemetry cable} to the laptop or desktop which is already connected to the Pixhawk. At this point, the ESCs are already booted, and this secondary connection ensures reliable communication with the flight controller.
    \item \textbf{Wait for the telemetry device} to show a green light. Then, you may disconnect the data cable. You should see a prompt on the QGroundControl (QGC) terminal indicating that the drone has switched to the secondary (telemetry) connection.
    \item \textbf{Reboot the software from QGC} - go to vehicle setup - go to parameters/tools and click reboot vehicle.
    \item The drone is now ready for takeoff. You may fly it manually or select from various available flight modes (e.g., \textit{Position}, \textit{Hold}, \textit{Altitude}, \textit{Acro}, etc.).
\end{enumerate}

\section{Flight Modes}

\subsection{Manual Mode}
When using \textbf{Manual Mode}, ensure that the knob on the RadioMaster (used for selecting modes) is set accordingly. Make sure the throttle is set to zero on the radio controller on arming the drone. Control the throttle, roll, pitch, and yaw using your radio controller. This mode provides direct control of the drone’s flight attitude.

\subsection{Position Mode}
\textbf{Position Mode} allows waypoint navigation across multiple points. Either visually select or give the global coordinates of the points to be traversed. if no waypoints are specified then the drone will stay at the current coordinate. The drone will then automatically traverse the waypoints in sequence.

\section{Takeoff Command}
To command the drone to take off:
\begin{enumerate}
    \item open Analyze Tools$>>$Mavlink console on the QGC GUI.
    \item Type the \verb|commander takeoff <height>| command. This will initiate an automatic takeoff procedure to the specified \texttt{<height>} in meters.

\end{enumerate}

\section{Pre-Startup Checks}

\begin{enumerate}
    \item Ensure that all the ESCs are properly connected to the power distribution board. Ensure that they are connected to the flight controller channels properly as well. The channels of the Pixhawk Cube must be mapped to the drone motors on the QGC and the same channel mapping must be followed while making the connections.
    \item Ensure all sensor calibrations are completed on the QGC. This is not a recurrent task but it is good practice to check the calibration before every flight, specially when the drone is used in different environments.
    \item All the propellers must be properly mounted and secured. They must all be of the same size, pitch and must be centrally balanced while attaching them to the motors. This is key to ensure that the drone does not flip over during takeoff.
    \item Check for loose connections and wires if any. These must be secured properly before the flight and to avoid any disconnections during the flight and to avoid any entanglement with the propellers.
    \item For the water spraying assembly, ensure that the pump is working properly and the connection from the motor driver to the pixhawk is secure. Check the system to ensure there are no leaks in the water tank and the water is not leaking into the drone body. The pump must be connected to the water tank and the water must be filled to the required level before the flight. 
    \item Check that the battery is fully charged and properly connected to the drone. The battery must be secured properly to avoid any disconnections during the flight. The battery must be of the same voltage and capacity as specified in the specifications of the drone.
    \item Check the radio controller to ensure that it is properly connected to the drone and the channels are mapped correctly. The radio controller must be of the same frequency as specified in the specifications of the drone.
\end{enumerate}

\section{Conclusion}
With this setup, you can flexibly control the drone using manual inputs, or leverage automated waypoint navigation. Always maintain safety checks and follow the recommended calibration procedures before every flight.

\end{document}
